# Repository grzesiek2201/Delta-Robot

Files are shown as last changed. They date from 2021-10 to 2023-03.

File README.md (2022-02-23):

# DIY Delta robot

## For your daily needs

**This repo gives a brief (for now) explanation about designing, modeling, building, wiring and programming delta type robot.**

### What does this repository include?
- Application controlling the robot with **live visualization** of the kinematics written in Python
- 3D model of the whole robot, as well as 3D models of all the parts that need to be printed
- BOM
- Build instructions
- Inverse and Forward Kinematics equations with derivation

### Features
- Both online and offline working mode - in offline you can simulate the robot's configuration in different positions
- Bluetooth connection
- Basic manual control by providing x,y,z coordiantes or  \theta_1, \theta_2, \theta_3
- Basic relative position control in Jog mode
- Enabling/disabling motors
- Starting/stoping the program
- Encoders calibration
- Homing
- Changing TCP offset and Jog step
- Changing Z axis limit
- Live robot kinematics visualization
- Live TCP displacement plot in x,y,z coordinates
- Live joints displacement plot in angular coordinates
- Creating and manipulating robot programs, saving, opening and editing. Points can be set either by manually typing in the coordinates or by a teach-in method, in which you hold the robot in a certain position and take it's current configuration as a point's coordiante

### Pictures and screenshots presenting the robot and application
Main screen             |  Collision detection
:-------------------------:|:-------------------------:
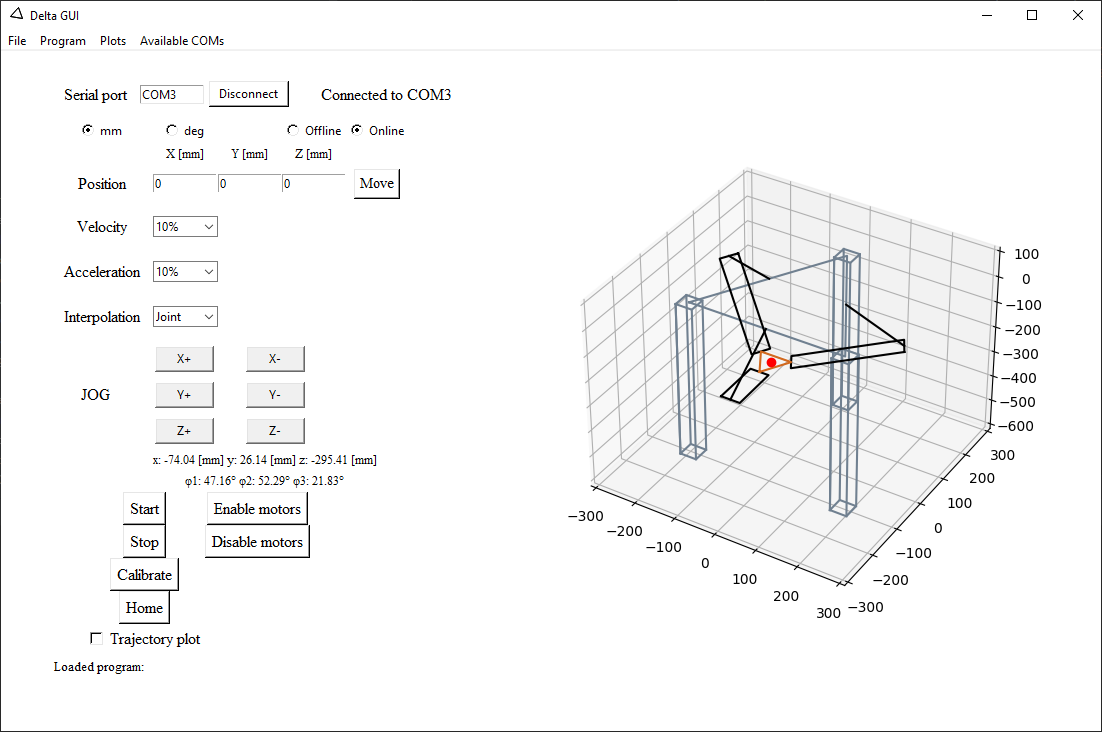
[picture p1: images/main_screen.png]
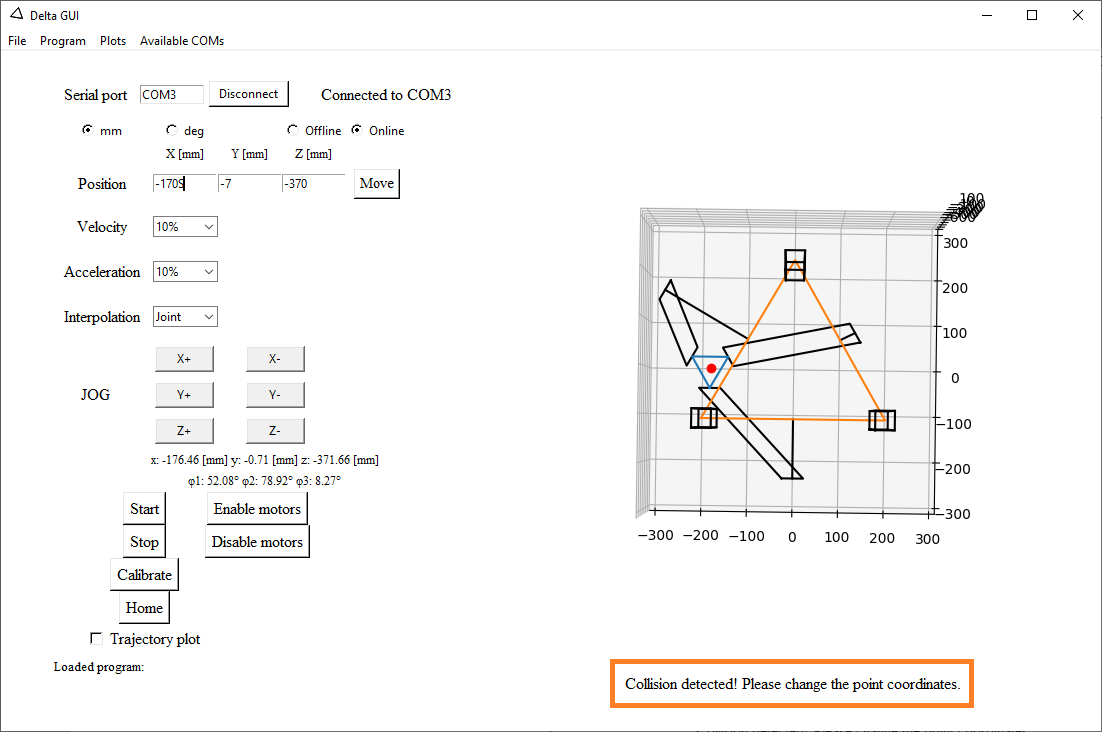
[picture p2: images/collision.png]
  |  
Work envelope             |  Real robot
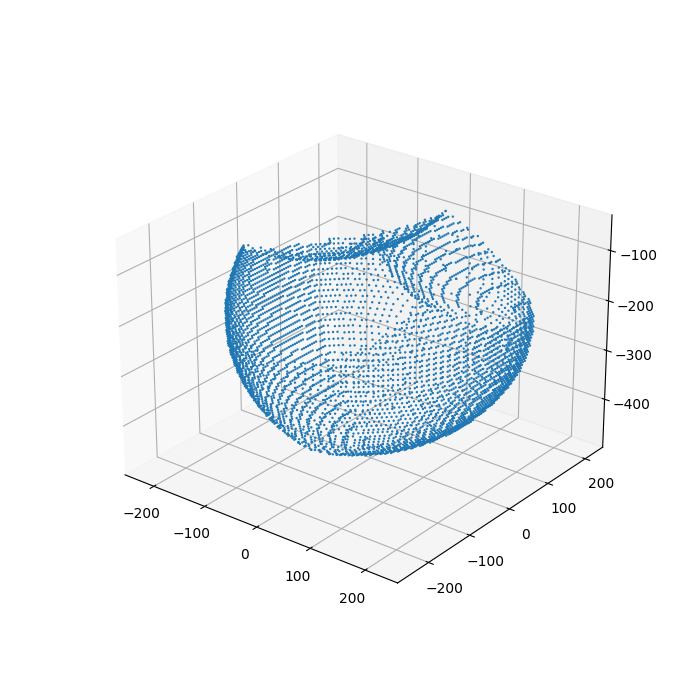
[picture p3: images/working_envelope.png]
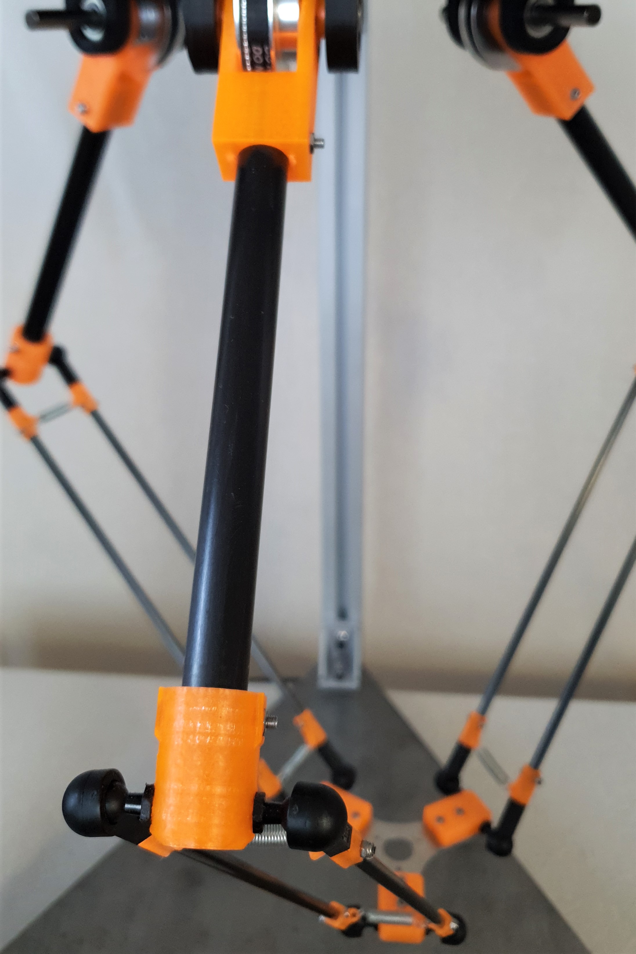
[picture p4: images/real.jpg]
  |  
Joints plot             |  Program creator
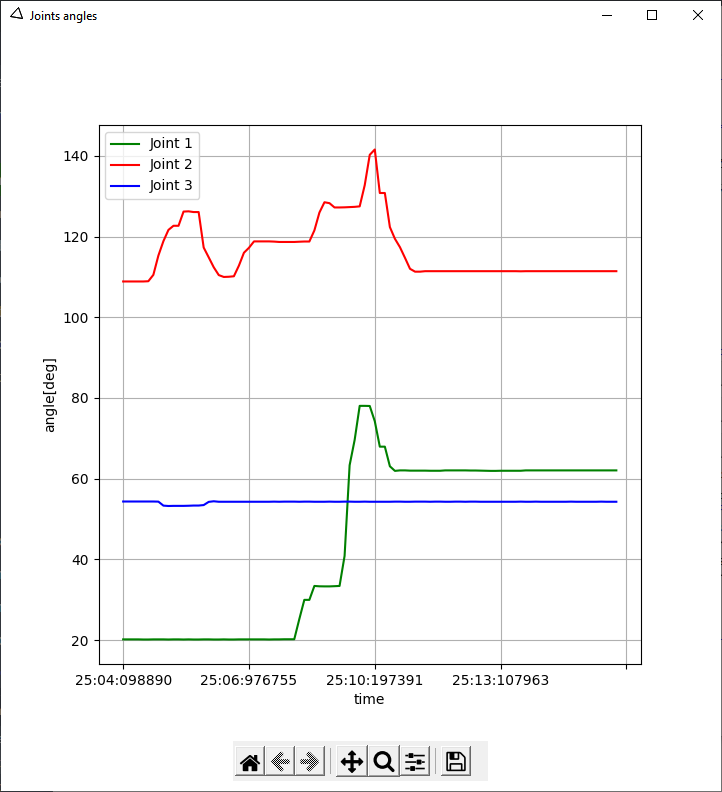
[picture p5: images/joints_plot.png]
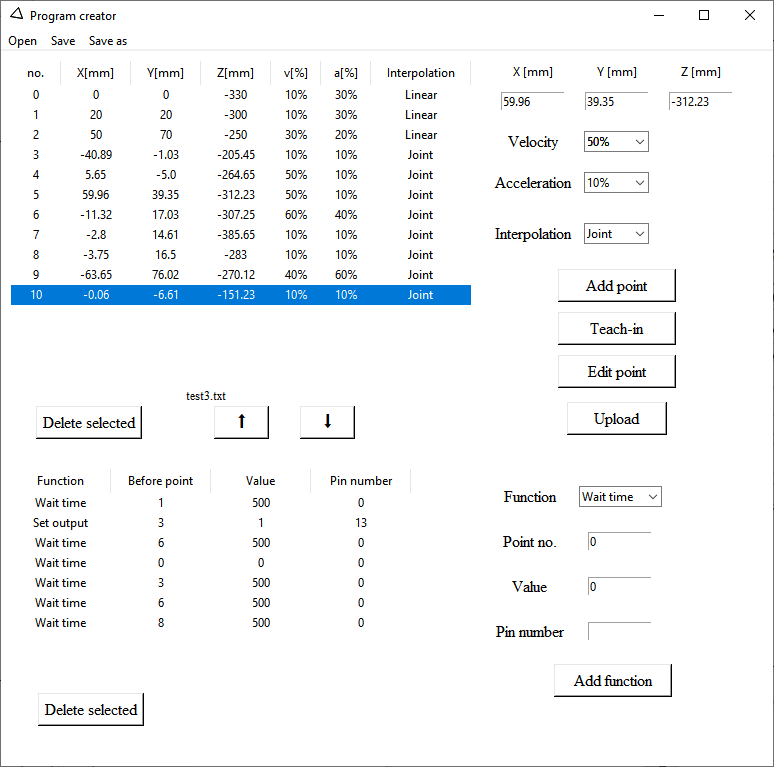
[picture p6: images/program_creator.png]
  |  
Kinematics drawing
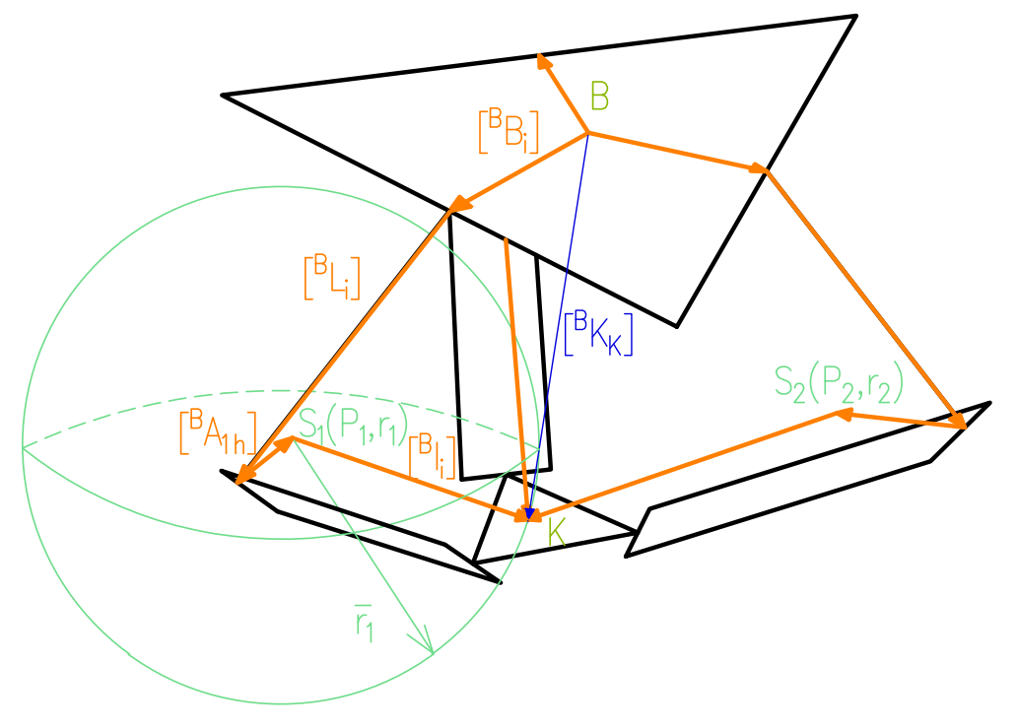
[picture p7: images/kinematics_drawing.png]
 |

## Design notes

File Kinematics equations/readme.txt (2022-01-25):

Kinematics equations necessary to build up the movement and visualization. Both Forward Kinematics and Inverse Kinematics are required.
The required equations are derived in the pdf document.
https://docs.google.com/viewer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

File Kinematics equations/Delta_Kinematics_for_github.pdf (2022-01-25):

# Delta Kinematics for the Delta Robot Project

grzesiek2201

January 2022

## Inverse Kinematics

As inverse kinematics is easier with parallel robots, we’ll start from them. They are also essential for robot control, unlike forward kinematics. The inverse kinematics problem states as follows: given a set of coordinates, find motor angles that correspond to them.

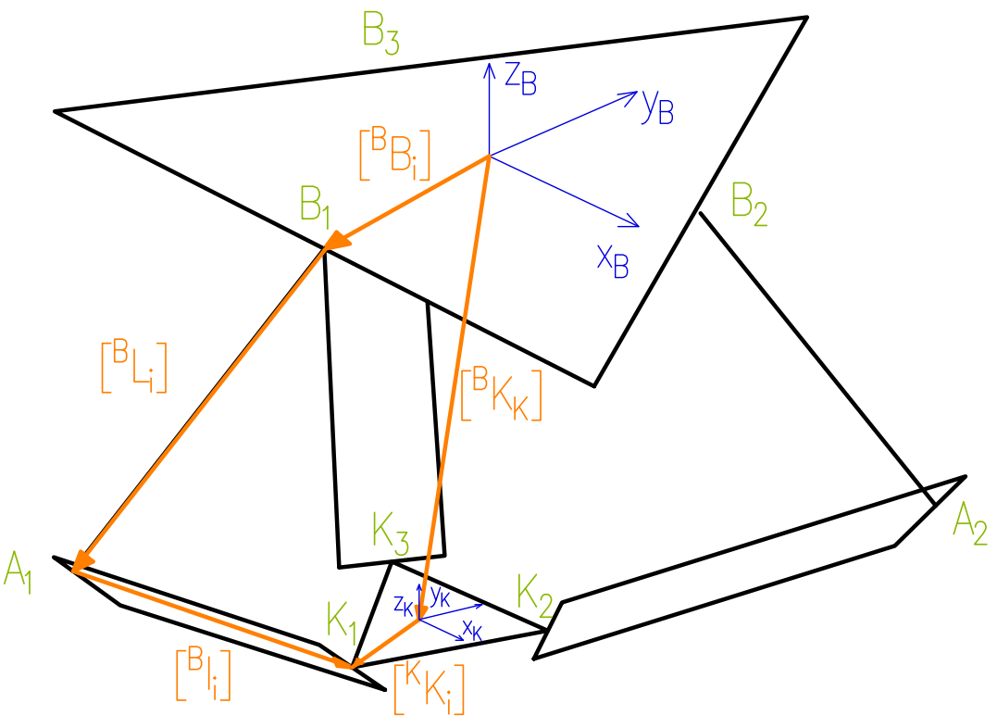
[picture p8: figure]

Figure 1: Kinematic structure of the robot. You can see two coordinate frames, one for the base(B) and one for the effector(K). Vectors drawn will be used in the vector-loop closure equations.

Vector-loop closure equation is as follows:

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
but there is no rotation in the effector

B
KR
= [I3] ,

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
BKK = [x, y, z]

T
(3)

KK1 =

0
−uK
0

KK2 =

sK
2
wK
0

KK3 =

−

sK
2
wK
0
- (4)

BB1 =

0
−wB
0

BB2 =

√
3
2 wB
1
2wB
0

BB3 =

−

√
3
2 wB
1
2wB
0
- (5)

BL1 =

0
−Lcos (θ1)
−Lsin (θ1)

BL2 =

√
3
2

Lcos (θ2)
1/2 Lcos (θ2)
−Lsin (θ2)

BL3 =

−

√
3
2

Lcos (θ3)
1/2 Lcos (θ3)
−Lsin (θ3)
- . | (6)

After substituting (3), (4), (5), (6) into (2):

Bl1 =

x
y + Lcos (θ1) + a
z + Lsin (θ1)

Bl2 =

x −

√
3
2

Lcos (θ2) + b
y −
1/2 Lcos (θ2) + c
z + Lsin (θ2)

Bl3 =

x +

√
3
2

Lcos (θ3) − b
y −

1/2 Lcos (θ3) + c
z + Lsin (θ3)
- ,

where

a = wB − uK, b =

sK
2

−

√
3
2

wB, c = wK −

1
2

wB.

It will be easier to square the vector’s modulus

l

2
i =

Bli

2
= l

2
ix + l

2
iy + l

2
iz.

After substitution we get

x

2 + y

2 + z

2 + L

2 + a

2 + 2ya − l

2 + 2L(y + a) cos θ1 + 2zLsin θ1 = 0 x

2 + y

2 + z

2 + L

2 + b

2 + c

2 + 2xb + 2yc − l

2 − L(

√
3(x + b) + y + c) cos θ2 + 2zLsin θ2 = 0 x

2 + y

2 + z

2 + L

2 + b

2 + c

2 − 2xb + 2yc − l

2 + L(

√
3(x − b) − y − c) cos θ3 + 2zLsin θ3 = 0.

The above system of equations can be simplified into

Ei cos θi + Fi sin θi + Gi = 0,

where:
E1 = 2L(y + a),

E2 = −L(

√
3(x + b) + y + c),

E3 = L(

√
3(x − y − b − c),
F1 = 2zL, | F2 = 2zL, | F3 = 2zL,

G1 = x

2 + y

2 + z

| 2 + L 2 + a | 2 + 2ya − l

2
,

G2 = x

2 + y

2 + z

2 + L

| 2 + b 2 + c | 2 + 2xb + 2yc − l

2
,

G3 = x

2 + y

2 + z

2 + L

| 2 + b 2 + c | 2 − 2xb + 2yc − l

2

The equations can be solved using Weierstrass substitution

Ei

1 − t

2
i
1 + t

2
i
| + Fi
| 2ti 1 + t

2
i
| | + Gi = 0,

Ei(1 − t

2
i

) + Fi(2ti) + Gi(1 + t

2
i

) = 0,

t

2
i

(Gi − Ei) + ti(2Fi) + (Gi + Ei) = 0.

Solution to the quadratic equation:

t1,2 =

−Fi ±

p
G²
i + F

2

i + E²
i
Gi − Ei

,

We get the solution to the inverse kinematics problem:

Θi = 2arctg(ti). | (7)

## Forward Kinematics

The forward kinematics problem states as follows: given a set of motor angles, find effector coordiantes that correspond to them. In order to find a solution to this problem, we must find points of intersection of three spheres, centers of which are located at the elbow joints transposed by the vectors -

BAih
and
radia of which are equal to the length of the forearms. Intersection points are the solution to the forward kinematics problem. The diagram is shown in the Figure 2.
Vectors -

BAih
are equal to:

BA1h =

0
−wB − Lcos(θ1) + uK
−Lsin(θ1)
- ,

BA2h =

√
3
2

(wB + Lcos(θ2)) −

sK
2
1/2(wB + Lcos(θ2)) − wK
−Lsin(θ2)
- ,

BA3h =

−

√
3
2

(wB + Lcos(θ3)) + sK
2
1/2(wB + Lcos(θ3)) − wK
−Lsin(θ3)
- . | (8)

There are three spheres: S1(P1, r1) S2(P2, r2) S3(P3, r3), where points Pi are known and equal to:

P1 =

x1
y1
z1
- , P2 =

x2
y2
z2
- , P3 =

x3
y3
z3

The system of equations describing the presented issue looks as follows:

(x − x1)

2 + (y − y1)

2 + (z − z1)

2 = r

2
1
(x − x2)

2 + (y − y2)

2 + (z − z2)

2 = r

2
2
(x − x3)

2 + (y − y3)

2 + (z − z3)

2 = r

2
3

, K =

x
y
z
- . | (9)


Figure 2: Kinematic diagram with vectors and spheres drawn in order to solve forward kinematics.

After expanding we must substract third equation from the first and second equation, result of which is the system of equations:
a11x + a12y + a13z = b1
a21x + a22y + a23z = b2

,

gdzie
a11 = 2(x3 − x1), | a12 = 2(y3 − y1), | a13 = 2(z3 − z1),
a21 = 2(x3 − x2), | a22 = 2(y3 − y2), | a23 = 2(z3 = z2),

b1 = r

2
1 − r

2
3 − x

2
1 − y

2
1 − z

2
1 + x

2
3 + y

2
3 + z

2/3, b2 = r

2
2 − r

2
3 − x

2
2 − y

2
2 − z

2
2 + x

2
3 + y

2
3 + z

2/3.

The above system of equations has been solved by determining z:

z =

b1
a13
− | a12 a13 y −

a11
a13

x

z =

b2
a23
− | a22 a23 y −

a21
a23

x

(10)

After substracting second equation from the first equation:

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
where
a1 =

a11

a13

−

a21

a23

, a2 =

a22

a23

−

a12

a13

, a3 =

b1

a13

−

b2
a23

We get
x = f(y) = a4y + a5,

where
a4 =

a2
a1

, a5 =

a3
a1

The dependency of x(y) has been determined. Next we need to substitute it into one of the equations in the (10). We get:
z = f(y) = a6y + a7,

where
a6 =

−a21a4 − a22

a23

, a7 =

b2 − a21a5

a23

The dependency z(y) has been determined, so we need to substitue it into one of the sphere equations. We get
ay² + by + c = 0, | (11)

where

a = a

2
4 + 1 + a

2/6, b = 2a4(a5 − a1) + 2a6(a7 − z1) − 2y1,

c = a5(a5 − 2x1) + a7(a7 − 2z1) + x

| 2 1 + y
| 2 1 + z
| 2 1 − r 2/1.

The equation (11) is an quadratic formula, solution to which is as follows:

x+ = a4y+ + a5

y+ =

−b+

√
b

2−4ac
2a

z+ = a6y+ + a7

,

x− = a4y− + a5

y− =

−b−

√
b

2−4ac
2a

z− = a6y− + a7

,

K+ =

x+
y+
z+
- , K− =

x−
y−
z−

In order for the real solutions to exist, the ∆ ≥ 0 must exist. If calculated ∆ will be smaller than zero, it suggests that an error occured when reading the motor angles, as motor angles cannot have irrational values.
Now we need to consider singularities of the given solution. It has no solutions, when at least one of the below condition is met:
a13 = 0, | (12)

a23 = 0, | (13)
a1 = 0, | (14)
a = 0. | (15)

Condition (14) is met, when

a1 =

a11

a13

−

a21

a23

=

(x3 − x1)(z3 − z2) − (x3 − x2)(z3 − z1) (z3 − z1)(z3 − z2)

= 0

⇕
x3 − x1
z3 = z1

=

x3 − x2
z3 − z2

Let z3 = x3 = 0 , so the point 3 lies in the middle of the coordinate system. Then x1
z1

=

x2
z2

This condition is only met when three points, which are the centers of the spheres, are collinear in the XZ plane. That is why for a valid geometry, this singularity never occurs.
Condition (15) is met, when

a = a

2
4 + a

2
6 + 1 = 0 ⇔ a

2
4 + a

2
6 = −1.

For real a4 and a6 this condition cannot be met, that is why it does not have to be considered in the overall solution.
Conditions (12) and (13) are met, when z3 − z1 = 0 and z3 − z2 = 0. It is only possible in a configuration in which the angle of the first arm is equal to the angle of the third arm and when angle of the second arm is equal to the angle of the third arm. This is possible under typical operation and has to be accounted for in the general solution. In order to get rid of the singularities the solution to the problem, when z1 = z2 = z3 =: zn, has been found. We start from the same equations for the intersection of three spheres as before

(x − x1)

2 + (y − y1)

2 + (z − zn)

2 = r

2
1
(x − x2)

2 + (y − y2)

2 + (z − zn)

2 = r

2
2
(x − x3)

2 + (y − y3)

2 + (z − zn)

2 = r
2/3.

After multiplication and substitution of the third equation for the first and the second equation we get
ax + by = c
dx + ey = f

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
af−cd
ae−bd

⇒

(
x =

ce−bf
ae−bd
y =

af−cd
ae−bd ,

where
a = 2(x3 − x1), | b = 2(y3 = y1), | c = r
| | 2 1 − r

2
3 − x

2
1 − y

2
1 + x

2
3 + y

2/3,

d = 2(x3 − x2), | e = 2(y3 − y2), | f = r

2
2 − r

2
3 − x

2
2 − y

2
2 + x

2
3 + y

2/3.

The calculated x and y have been substituted into the first equation from the 9 system of equations:

Az² + Bz + C = 0,

where
| A = 1,
B = −2zn,
| C = x 2 + y 2 + x
| 2 1 + y

2
| | 1 − 2xx1 − r

2
1 + z

2
n

The solution to the forward kinematics problem is as follows:

x =

ce−bf
ad−bd

y =

af−cd
ae−bd

z =

−B±

√
B²−4C

We also have to investigate the singularities of the solution:

ae − bd = 0,
∆ < 0 ⇔ B² − 4AC = 0.

The first of the singularities has been expanded below:

ae − bd = 0 ⇔ x3−x1
y3−y1

=

x3−x2
y3−y2

The above equality is met only when centers of the spheres lay on the XY plane and are collinear. For a symmetric configuration of the robot, this singularity does not have to be considered in the general solution.
The second of the singularities is met when

B

2 − 4AC = 0 ⇔ r

2
1 < (x − x1)

2 + (y − y1)

2

The above inequality cannot be met, as we know the the below equation is true

(x − x1)

2 + (y − y1)

2 = r
2/1.

There is also a situation in which two of the three spheres are position on the same height. Instead of deriving further equations, which would let us get rid of this singularity, it is possible to add a very small value to one of the sphere’s height when the situation occurs. It does not influence the accuracy of the visualization and control in a visible way, but it does simplify the theoretical considerations.

## Visualization

The calculation will based on the angular position of the motors measured by enoders as well as equations derived below. In order to create the visualization, we must know coordinates of all the points of a drawn line. Objects that will be drawn as a line are: each of the arms, each of the forearms, base, and effector. Each of the legs will be a simple prism, thus their representation will consist of two bases and four edges. The base vertices are described with vectors

Bb1 =

sB
2
−wB
0
- ,

Bb2 =

0
uK
0
- ,

Bb3 =

−

sB
2
−wB
0
- . | (16)

The vectors below -
BAi
are describing position of the elbow joints in respect to the base B:

BA1 =

0
−wB − Lcos(θ1)
−Lsin(θ1)
- ,

BA2 =

√
3
2

(wB + Lcos(θ2))
1/2(wB + Lcos(θ2))
−Lsin(θ2)
- ,

BA3 =

−

√
3
2

(wB + Lcos(θ3))
1/2(wB + Lcos(θ3))
−Lsin(θ3)
- . | (17)

Vectors -
BKi
describe the position of the effector’s joints in respect to the base B:

BK1 =

x
−

sK
2 + y
z
- ,

BK2 =

sK
2 + x
wK + y
z
- ,

BK3 =

−

sK
2 + x
wK + y
z
- . | (18)

Vectors -
BBi
describe the position of the arm joints in respect to the base B:

BB1 =

0
−wB
0
- ,

BB2 =

√
3
2 wB
1
2wB
0
- ,

BB3 =

−

√
3
2 wB
1
2wB
0
- . | (19)

Vectors -

BAij
describe the position of the elbow joints transposed by a vector equal to their width, in respect to the base B:

BA11 =

−

ew
2
−wB − Lcos(θ1)
−Lsin(θ1)
- ,

BA12 =

ew
2
−wB − Lcos(θ1)
−Lsin(θ1)
- ,

BA21 =

√
3
2

(wB + Lcos(θ2)) + ew
4
1/2(wB + Lcos(θ2)) −

√
3
4

ew
−Lsin(θ2)

- ,

BA22 =

√
3
2

(wB + Lcos(θ2)) −

ew
4
1/2(wB + Lcos(θ2)) +

√
3
4

ew
−Lsin(θ2)

- ,

BA31 =

−

√
3
2

(wB + Lcos(θ3)) + ew
4
1/2(wB + Lcos(θ3)) +

√
3
4

ew
−Lsin(θ3)

- ,

BA32 =

−

√
3
2

(wB + Lcos(θ3)) −

ew
4
1/2(wB + Lcos(θ3)) −

√
3
4

ew
−Lsin(θ3)

Vectors -
BKij
describe the position of the efector joints transpoed by the same vector as above, in respect to the base B:

BK11 =

x −

ew
2
−

sK
2 + y
z
- ,

BK12 =

x +

ew
2
−

sK
2 + y
z
- ,

BK21 =

sK
2 + x +

ew
4
wK + y −

√
3
4

ew
z
- ,

BK21 =

sK
2 + x −

ew
4
wK + y +

√
3
4

ew
z
- ,

BK31 =

−

sK
2 + x +

ew
4
wK + y +

√
3
4

ew
z
- ,

BK32 =

−

sK
2 + x −

ew
4
wK + y −

√
3
4

ew
z

We know all the points necessary to create the visualization of the kinematic structure of the robot.

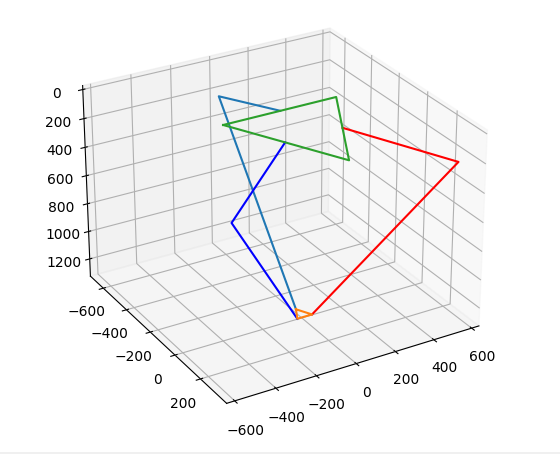
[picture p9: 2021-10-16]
DeltaApp/src/plot_example.png

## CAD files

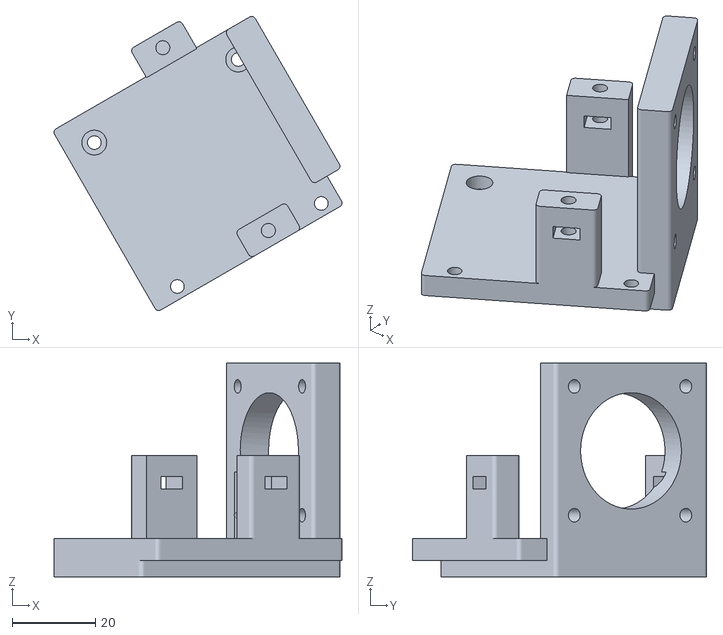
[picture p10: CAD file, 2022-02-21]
stl_dxf/motor_mount.stl
69.3 x 70.8 x 51.5

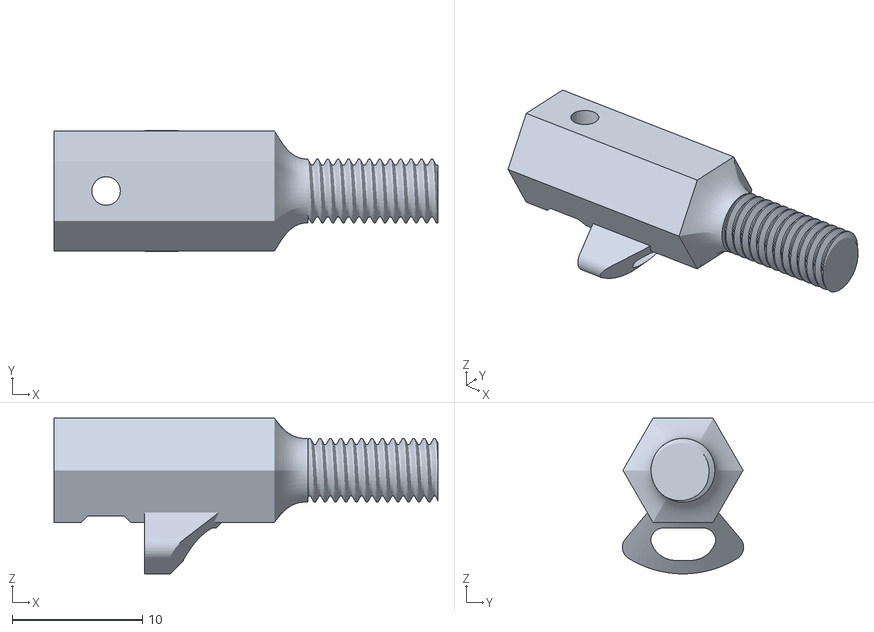
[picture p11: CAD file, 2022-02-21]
stl_dxf/elbow_joint_1.stl
29.5 x 9.32 x 12.0

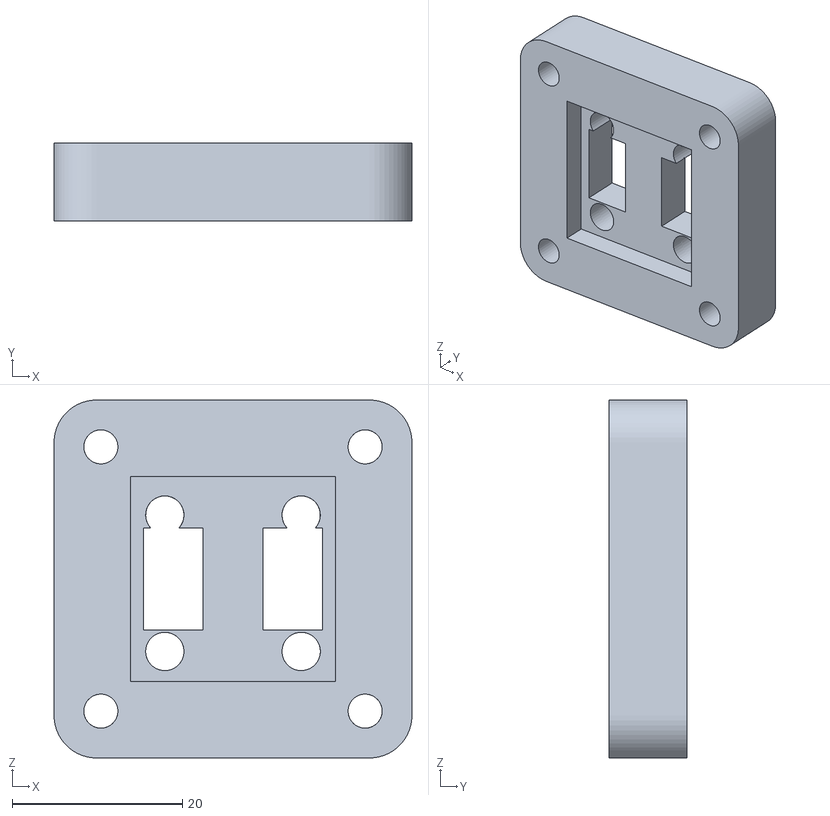
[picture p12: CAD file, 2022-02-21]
stl_dxf/as5600_encoder_mount.stl
42.0 x 9.20 x 42.0

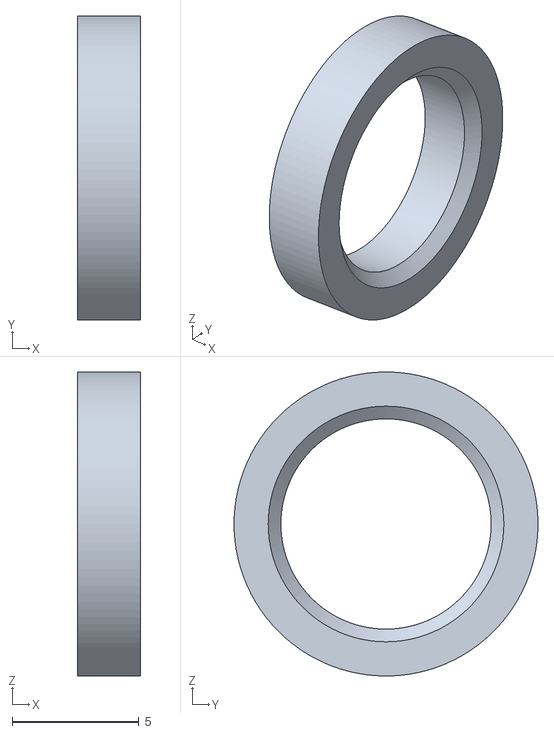
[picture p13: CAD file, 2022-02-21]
stl_dxf/shoulder_mount_spacer.stl
2.50 x 12.0 x 12.0

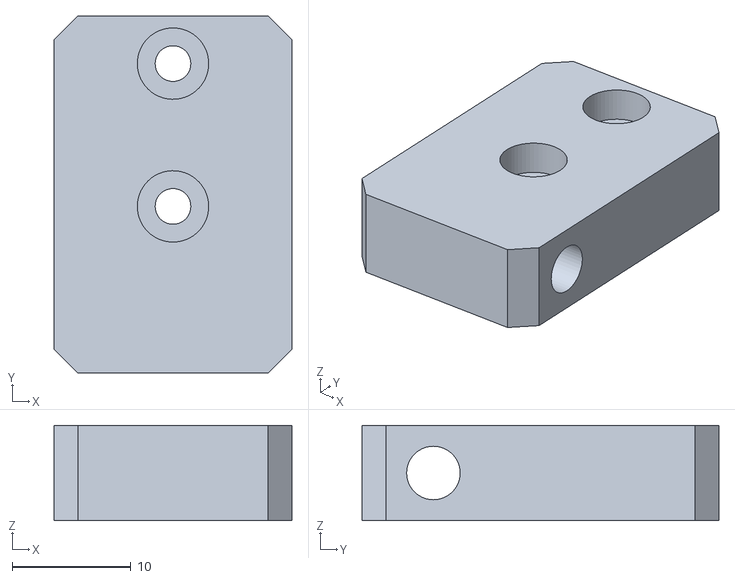
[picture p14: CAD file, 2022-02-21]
stl_dxf/effector_forearm_mounting.stl
20.0 x 30.0 x 8.00

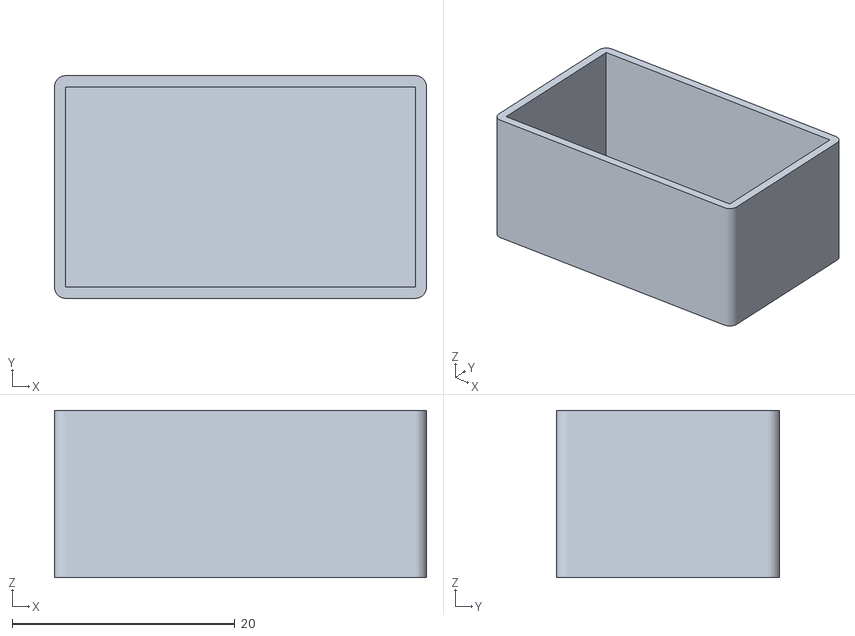
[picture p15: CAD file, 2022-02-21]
stl_dxf/multiplexer_enclosure.stl
33.4 x 20.0 x 15.0

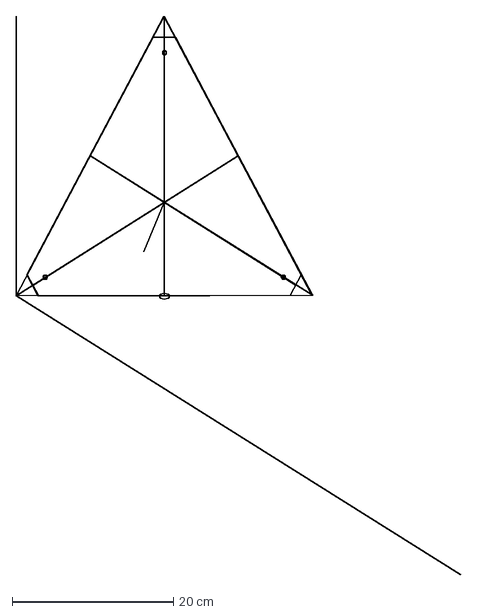
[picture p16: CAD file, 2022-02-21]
stl_dxf/top_plate.dxf
55.1 x 69.3 cm

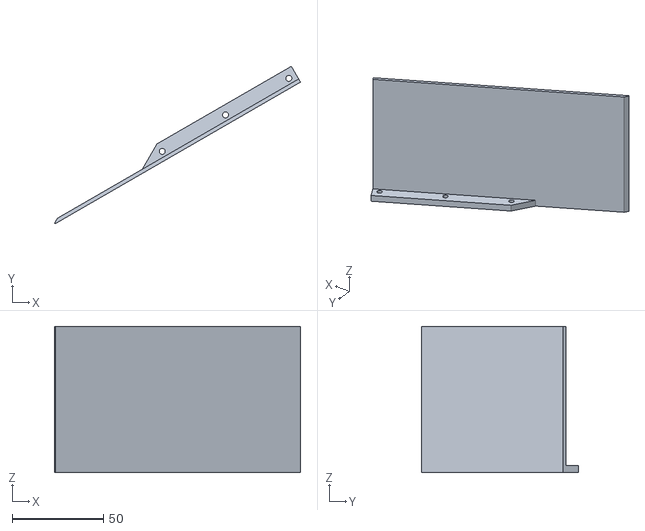
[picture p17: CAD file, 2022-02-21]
stl_dxf/wall_no_fan.stl
134.7 x 86.2 x 80.0

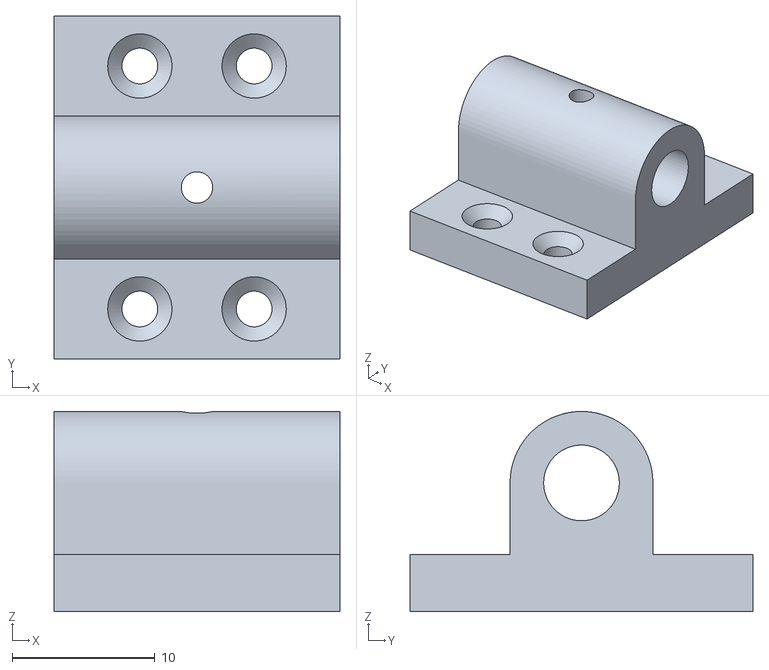
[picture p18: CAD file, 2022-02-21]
stl_dxf/carbon_tube_holder_opened.stl
20.0 x 24.0 x 14.0

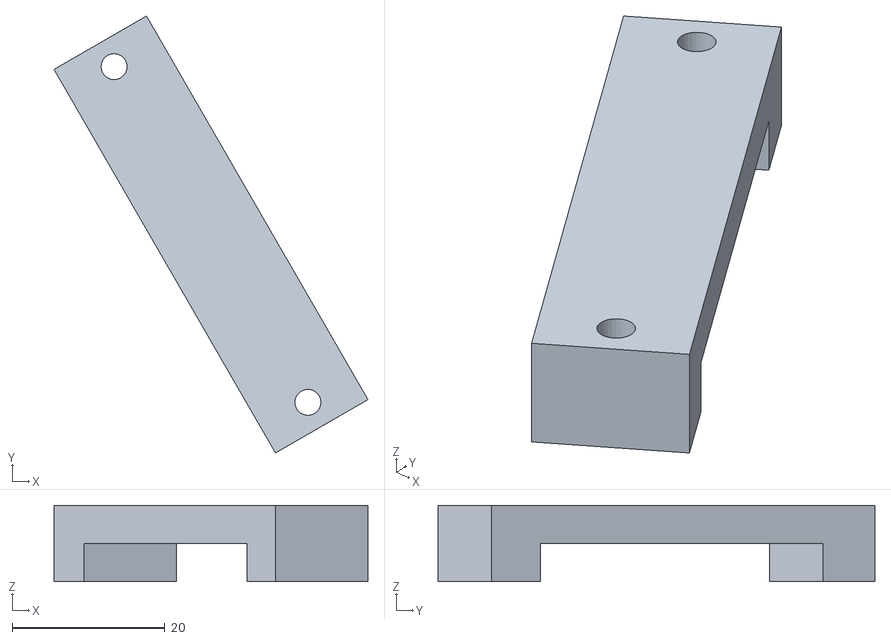
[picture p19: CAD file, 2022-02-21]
stl_dxf/motor_mount_holder.stl
41.1 x 57.3 x 10.0

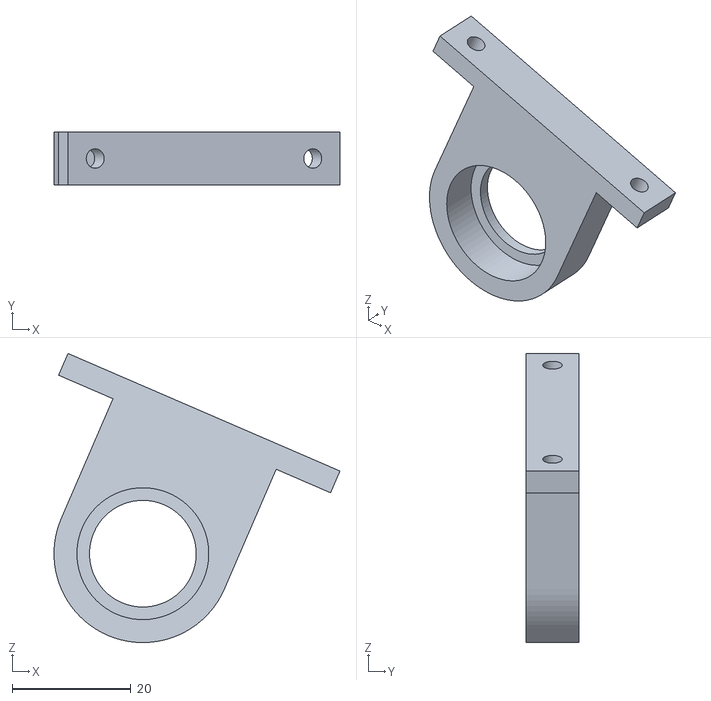
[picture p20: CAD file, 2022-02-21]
stl_dxf/bearing_mount.stl
48.3 x 9.00 x 48.8

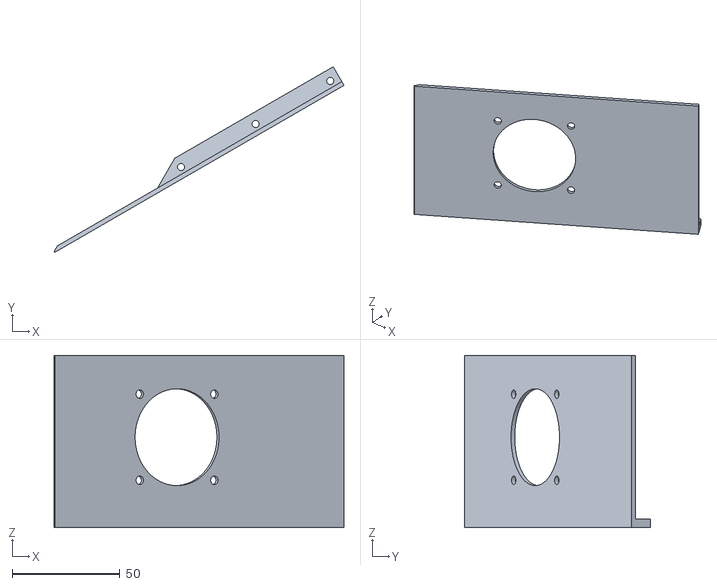
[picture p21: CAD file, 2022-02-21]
stl_dxf/wall_w_fan_1.stl
134.7 x 86.2 x 80.0

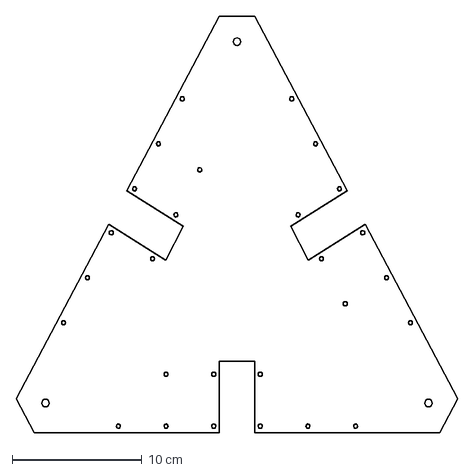
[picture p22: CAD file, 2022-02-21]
stl_dxf/bottom_plate.dxf
34.0 x 32.0 cm

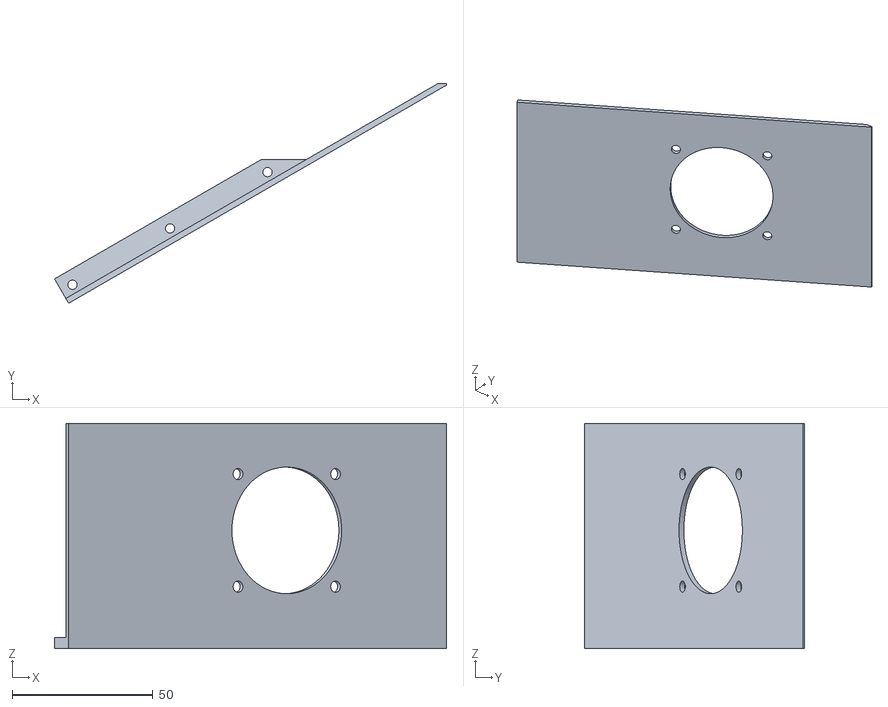
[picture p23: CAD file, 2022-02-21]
stl_dxf/wall_w_fan_2.stl
139.2 x 78.0 x 80.0

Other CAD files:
stl_dxf/effector_plate.dxf
stl_dxf/shoulder_mount.stl
stl_dxf/carbon_tube_holder_closed.stl
stl_dxf/elbow_joint_2.stl

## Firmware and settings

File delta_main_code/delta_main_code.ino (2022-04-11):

#include <ArduinoJson.h>
#include <Wire.h>
#include "inverse_kin.h"

#include "SSD1306Ascii.h"
#include "SSD1306AsciiAvrI2c.h"

#include "FlexyStepper.h"
#include <SPI.h>
#include <SD.h>

StaticJsonDocument<64> doc_rx;
StaticJsonDocument<64> doc_tx;
char output[64];

// oled
#define RST_PIN -1
#define OLED_PIN 4
SSD1306AsciiAvrI2c oled;

#define TIMEOUT 5000
#define BAUDRATE 115200

#define ENC_COMPENSATE_1 120
#define ENC_COMPENSATE_2 148
#define ENC_COMPENSATE_3 158

#define TCAADDR 0x70
#define address 0x36

#define NO_POINTS 50

#define SERVO_PIN 63

// flexystepper
FlexyStepper stepper1;
FlexyStepper stepper2;
FlexyStepper stepper3;

// SD card
File my_file;
String buffer;
// #define INTERVALS_SIZE 400
// int velocities_1[INTERVALS_SIZE];
// int velocities_2[INTERVALS_SIZE];
// int velocities_3[INTERVALS_SIZE];
int velocities[3];

// reading messages
const byte numChars = 128;
char receivedChars[numChars];
boolean newData = false;

// communication
uint8_t index_of_point;
uint8_t interpolation_array[NO_POINTS];
uint8_t velocity_array[NO_POINTS];
uint8_t acceleration_array[NO_POINTS];
float x_array[NO_POINTS];
float y_array[NO_POINTS];
float z_array[NO_POINTS];

// additional functions
bool start = false;
bool teach_in_cmd = false;
uint8_t enable_cmd = 0;
uint8_t gripper_state = 0;
uint16_t program_length = 0;
byte mode = 0;
bool receive_in_progress = false;

// inverse kinematics
inverse_kin inverse_kin;
float position_array[3];
float previous_fi_array[3];
float fi_array[3];
short int steps_to_make_x[NO_POINTS];
short int steps_to_make_y[NO_POINTS];
short int steps_to_make_z[NO_POINTS];

// encoders
int low_byte;                        //raw angle 7:0
word high_byte;                      //raw angle 7:0 and 11:8
int raw_angle;                       //final raw angle
float deg_angle[3];                     //raw angle in degrees (360/4096 * [value between 0-4095])

int quadrantNumber[3], previousquadrantNumber[3]; //quadrant IDs
float numberofTurns[3] = {0, 0, 0}; //number of turns
float correctedAngle[3] = {0, 0, 0}; //tared angle - based on the startup value
float startAngle[3] = {0, 0, 0}; //starting angle
float totalAngle[3] = {0, 0, 0}; //total absolute angular displacement
float previoustotalAngle[3] = {0, 0, 0}; //for the display printing


// For RAMPS 1.4
#define X_DIR_PIN          55
#define X_STEP_PIN         54
#define X_ENABLE_PIN       38

#define Y_DIR_PIN          61
#define Y_STEP_PIN         60
#define Y_ENABLE_PIN       56

#define Z_DIR_PIN          48
#define Z_STEP_PIN         46
#define Z_ENABLE_PIN       62

#define X_STEP_HIGH             PORTF |=  0b00000001;
#define X_STEP_LOW              PORTF &= ~0b00000001;

#define Y_STEP_HIGH             PORTF |=  0b01000000;
#define Y_STEP_LOW              PORTF &= ~0b01000000;

#define Z_STEP_HIGH             PORTL |=  0b00001000;
#define Z_STEP_LOW              PORTL &= ~0b00001000;

#define TIMER1_INTERRUPTS_ON    TIMSK1 |=  (1 << OCIE1A);
#define TIMER1_INTERRUPTS_OFF   TIMSK1 &= ~(1 << OCIE1A);


struct stepperInfo {
  // externally defined parameters
  float acceleration;
  volatile unsigned long minStepInterval; // ie. max speed, smaller is faster
  void (*dirFunc)(int);
  void (*stepFunc)();

  // derived parameters
  unsigned int c0;                // step interval for first step, determines acceleration
  long stepPosition;              // current position of stepper (total of all movements taken so far)

  // per movement variables (only changed once per movement)
  volatile int dir;                        // current direction of movement, used to keep track of position
  volatile unsigned int totalSteps;        // number of steps requested for current movement
  volatile bool movementDone = false;      // true if the current movement has been completed (used by main program to wait for completion)
  volatile unsigned int rampUpStepCount;   // number of steps taken to reach either max speed, or half-way to the goal (will be zero until this number is known)
  volatile unsigned long estStepsToSpeed;  // estimated steps required to reach max speed
  volatile unsigned long estTimeForMove;   // estimated time (interrupt ticks) required to complete movement
  volatile unsigned long rampUpStepTime;
  volatile float speedScale;               // used to slow down this motor to make coordinated movement with other motors

  // per iteration variables (potentially changed every interrupt)
  volatile unsigned int n;                 // index in acceleration curve, used to calculate next interval
  volatile float d;                        // current interval length
  volatile unsigned long di;               // above variable truncated
  volatile unsigned int stepCount;         // number of steps completed in current movement
};

void xStep() {
  X_STEP_HIGH
  X_STEP_LOW
}
void xDir(int dir) {
  digitalWrite(X_DIR_PIN, dir);
}

void yStep() {
  Y_STEP_HIGH
  Y_STEP_LOW
}
void yDir(int dir) {
  digitalWrite(Y_DIR_PIN, dir);
}

void zStep() {
  Z_STEP_HIGH
  Z_STEP_LOW
}
void zDir(int dir) {
  digitalWrite(Z_DIR_PIN, dir);
}

void resetStepperInfo( stepperInfo& si ) {
  si.n = 0;
  si.d = 0;
  si.di = 0;
  si.stepCount = 0;
  si.rampUpStepCount = 0;
  si.rampUpStepTime = 0;
  si.totalSteps = 0;
  si.stepPosition = 0;
  si.movementDone = false;
}

#define NUM_STEPPERS 3

volatile stepperInfo steppers[NUM_STEPPERS];

struct pointFunction{
  bool func_type[3];
  unsigned int value[3];
  uint8_t pin_no[3];
};

void reset_point_functions(pointFunction* pt);
void reset_point_functions(pointFunction* pt){
  for(int i=0; i < NO_POINTS; i++){
    for(int j = 0; j < 3; j++){
      pt[i].func_type[j] = 0;
      pt[i].value[j] = 0;
      pt[i].pin_no[j] = 0;    
    } 
  }     
}

pointFunction point_functions[NO_POINTS];

void showOnScreen(String text, bool show_coordinates = 0, int number_of_coordinate = 0);

void setup() {
  Serial.begin(BAUDRATE);
  Serial2.begin(BAUDRATE);
  Wire.begin();

  //oled
  tcaselect(OLED_PIN);
  #if RST_PIN >= 0
  oled.begin(&Adafruit128x64, 0x3C, RST_PIN);
  #else // RST_PIN >= 0
  oled.begin(&Adafruit128x64, 0x3C);
  #endif // RST_PIN >= 0
  // Call oled.setI2cClock(frequency) to change from the default frequency.

  oled.setFont(Arial_bold_14);
  oled.clear();

  oled.set2X();
  showOnScreen("is delta");
  oled.set1X();

  // flexystepper
  stepper1.connectToPins(X_STEP_PIN, X_DIR_PIN);
  stepper2.connectToPins(Y_STEP_PIN, Y_DIR_PIN);
  stepper3.connectToPins(Z_STEP_PIN, Z_DIR_PIN);
  stepper1.setAccelerationInStepsPerSecondPerSecond(3000);
  stepper2.setAccelerationInStepsPerSecondPerSecond(3000);
  stepper3.setAccelerationInStepsPerSecondPerSecond(3000);
  
  // SD card
  uint16_t start_time = millis();
  uint16_t init_time = 0;
  uint8_t timeout = 2000;
  while(!SD.begin(53) && init_time < timeout)
    init_time = millis() - start_time;
  
  // readIntervals(velocities_1, velocities_2, velocities_3);  // read intervals from SD card


  startAngle[0] = ENC_COMPENSATE_1; 
  startAngle[1] = ENC_COMPENSATE_2; 
  startAngle[2] = ENC_COMPENSATE_3;

  readRawAngle(1);
  readRawAngle(2);  
  readRawAngle(3);   
  correctAngle(1);
  correctAngle(2);
  correctAngle(3);
  checkQuadrant(1);
  checkQuadrant(2);
  checkQuadrant(3);
  fi_array[0] = totalAngle[0];
  fi_array[1] = totalAngle[1];
  fi_array[2] = totalAngle[2];

  pinMode(X_STEP_PIN,   OUTPUT);
  pinMode(X_DIR_PIN,    OUTPUT);
  pinMode(X_ENABLE_PIN, OUTPUT);

  pinMode(Y_STEP_PIN,   OUTPUT);
  pinMode(Y_DIR_PIN,    OUTPUT);
  pinMode(Y_ENABLE_PIN, OUTPUT);

  pinMode(Z_STEP_PIN,   OUTPUT);
  pinMode(Z_DIR_PIN,    OUTPUT);
  pinMode(Z_ENABLE_PIN, OUTPUT);

  digitalWrite(X_ENABLE_PIN, HIGH);
  digitalWrite(Y_ENABLE_PIN, HIGH);
  digitalWrite(Z_ENABLE_PIN, HIGH);

  noInterrupts();
  TCCR1A = 0;
  TCCR1B = 0;
  TCNT1  = 0;

  OCR1A = 1000;                             // compare value
  TCCR1B |= (1 << WGM12);                   // CTC mode
  TCCR1B |= ((1 << CS11) | (1 << CS10));    // 64 prescaler
  interrupts();

  steppers[0].dirFunc = xDir;
  steppers[0].stepFunc = xStep;
  steppers[0].acceleration = 500;
  steppers[0].minStepInterval = 30;

  steppers[1].dirFunc = yDir;
  steppers[1].stepFunc = yStep;
  steppers[1].acceleration = 500;
  steppers[1].minStepInterval = 30;

  steppers[2].dirFunc = zDir;
  steppers[2].stepFunc = zStep;
  steppers[2].acceleration = 500;
  steppers[2].minStepInterval = 30;

  while(Serial2.available()){ 
    char clear_input = Serial2.read();
    }
}

void resetStepper(volatile stepperInfo& si) {
  si.c0 = si.acceleration;
  si.d = si.c0;
  si.di = si.d;
  si.stepCount = 0;
  si.n = 0;
  si.rampUpStepCount = 0;
  si.movementDone = false;
  si.speedScale = 1;

  float a = si.minStepInterval / (float)si.c0;
  a *= 0.676;

  float m = ((a*a - 1) / (-2 * a));
  float n = m * m;

  si.estStepsToSpeed = n;
}

volatile uint8_t remainingSteppersFlag = 0;

float getDurationOfAcceleration(volatile stepperInfo& s, unsigned int numSteps) {

  return s.c0 * sqrt(1.38 * numSteps + numSteps);
  
}

void prepareMovement(int whichMotor, long steps) {
  if (steps == 0) {return;}  
  volatile stepperInfo& si = steppers[whichMotor];
  si.dirFunc( steps < 0 ? HIGH : LOW );
  si.dir = steps > 0 ? 1 : -1;
  si.totalSteps = abs(steps);
  resetStepper(si);
  
  remainingSteppersFlag |= (1 << whichMotor);

  unsigned long stepsAbs = abs(steps);

  if ( (2 * si.estStepsToSpeed) < stepsAbs ) {
    // there will be a period of time at full speed
    unsigned long stepsAtFullSpeed = stepsAbs - 2 * si.estStepsToSpeed;
    float accelDecelTime = getDurationOfAcceleration(si, si.estStepsToSpeed);
    si.estTimeForMove = 2 * accelDecelTime + stepsAtFullSpeed * si.minStepInterval;
  }
  else {
    // will not reach full speed before needing to slow down again
    float accelDecelTime = getDurationOfAcceleration( si, stepsAbs / 2 );
    si.estTimeForMove = 2 * accelDecelTime;
  }
}

volatile uint8_t nextStepperFlag = 0;

void setNextInterruptInterval() {

  bool movementComplete = true;

  unsigned long mind = 999999;
  for (int i = 0; i < NUM_STEPPERS; i++) {
    if ( ((1 << i) & remainingSteppersFlag) && steppers[i].di < mind ) {
      mind = steppers[i].di;
    }
  }

  nextStepperFlag = 0;
  for (int i = 0; i < NUM_STEPPERS; i++) {
    if ( ! steppers[i].movementDone )
      movementComplete = false;
    if ( ((1 << i) & remainingSteppersFlag) && steppers[i].di == mind )
      nextStepperFlag |= (1 << i);
  }

  if ( remainingSteppersFlag == 0 ) {
    TIMER1_INTERRUPTS_OFF
    OCR1A = 65500;
  }

  OCR1A = mind;
}

ISR(TIMER1_COMPA_vect)
{
  unsigned int tmpCtr = OCR1A;

  OCR1A = 65500;

  for (int i = 0; i < NUM_STEPPERS; i++) {

    if ( ! ((1 << i) & remainingSteppersFlag) )
      continue;

    if ( ! (nextStepperFlag & (1 << i)) ) {
      steppers[i].di -= tmpCtr;
      continue;
    }

    volatile stepperInfo& s = steppers[i];

    if ( s.stepCount < s.totalSteps ) {
      s.stepFunc();
      s.stepCount++;
      s.stepPosition += s.dir;
      if ( s.stepCount >= s.totalSteps ) {
        s.movementDone = true;
        remainingSteppersFlag &= ~(1 << i);
      }
    }

    if ( s.rampUpStepCount == 0 ) {
      s.n++;
      s.d = s.d - (2 * s.d) / (4 * s.n + 1);
      if ( s.d <= s.minStepInterval ) {
        s.d = s.minStepInterval;
        s.rampUpStepCount = s.stepCount;
      }
      if ( s.stepCount >= s.totalSteps / 2 ) {
        s.rampUpStepCount = s.stepCount;
      }
      s.rampUpStepTime += s.d;
    }
    else if ( s.stepCount >= s.totalSteps - s.rampUpStepCount ) {
      s.d = (s.d * (4 * s.n + 1)) / (4 * s.n + 1 - 2);
      s.n--;
    }

    s.di = s.d * s.speedScale; // integer
  }

  setNextInterruptInterval();

  TCNT1  = 0;
}


void runAndWait() {
  adjustSpeedScales();
  setNextInterruptInterval();
  TIMER1_INTERRUPTS_ON
  while ( remainingSteppersFlag )
  {
    readEncoders();
    // delayMicroseconds(500000);
    sendEncodersData();
    // delayMicroseconds(1000);
  };
  remainingSteppersFlag = 0;
  nextStepperFlag = 0;
}

void adjustSpeedScales() {
  float maxTime = 0;
  
  for (int i = 0; i < NUM_STEPPERS; i++) {
    if ( ! ((1 << i) & remainingSteppersFlag) )
      continue;
    if ( steppers[i].estTimeForMove > maxTime )
      maxTime = steppers[i].estTimeForMove;
  }

  if ( maxTime != 0 ) {
    for (int i = 0; i < NUM_STEPPERS; i++) {
      if ( ! ( (1 << i) & remainingSteppersFlag) )
        continue;
      steppers[i].speedScale = maxTime / steppers[i].estTimeForMove;
    }
  }
}


void loop() {
  int8_t point_number = 0;
  readEncoders();
  sendEncodersData();
  fi_array[0] = totalAngle[0];
  fi_array[1] = totalAngle[1];
  fi_array[2] = totalAngle[2];
  unsigned long time = millis();
  unsigned long receive_time = millis();  
  do {
      mode = readMode();  // read the message mode
      if (mode >= '0'){   // if the message mode is an information message, process it
        receive_in_progress = true; // make sure all the message will be received
        delay(10);
        recvWithStartEndMarkers();  // read the message
        if (newData == true){ // if the message is read
          newData = false;  // reset the new data bool
          deserializeSerial();
          switch(mode) {
            case '0':
              start = doc_rx["start"];
              break;

            case '1': // read program's points
              {
              showOnScreen("Reading program...");             
              reset_point_functions(point_functions);   // reset additional functions              
              readPoint();
              Serial2.print("OK");
              Serial2.flush();
              }
              program_length = index_of_point + 1;              
              break;
            case '2': // manual move
              readPoint();

              showOnScreen("Moving to point ", 1, 0);
                           
              changeParameters(index_of_point);
              calculateSteps(index_of_point+1);
              prepareMovement(0, steps_to_make_x[index_of_point]);
              prepareMovement(1, steps_to_make_y[index_of_point]);
              prepareMovement(2, steps_to_make_z[index_of_point]);
              runAndWait();
              
              Serial2.print("OK");
              sendEncodersData();
              break;
            case '3': // Wait time         
              Serial2.print("OK");   
              point_number = doc_rx["pt_no"];
              point_functions[point_number].func_type[0] = 1;
              point_functions[point_number].value[0] = doc_rx["value"];
              //
              Serial.print("func_type[pt][0]="); Serial.println(point_functions[point_number].func_type[0]);
              Serial.print("value[pt][0]="); Serial.println(point_functions[point_number].value[0]);
              //             
              break;   
            case '4': // Wait input
              Serial2.print("OK");
              point_number = doc_rx["pt_no"];
              point_functions[point_number].func_type[1] = 1;
              point_functions[point_number].value[1] = doc_rx["value"];
              point_functions[point_number].pin_no[1] = doc_rx["pin_no"];
              //
              Serial.print("func_type[pt][1]="); Serial.println(point_functions[point_number].func_type[1]);
              Serial.print("value[pt][1]="); Serial.println(point_functions[point_number].value[1]);
              Serial.print("pin_no[pt][1]="); Serial.println(point_functions[point_number].pin_no[1]);
              //              
              break;            
            case '5': // Set output
              Serial2.print("OK");
              point_number = doc_rx["pt_no"];            
              point_functions[point_number].func_type[2] = 1;
              point_functions[point_number].value[2] = doc_rx["value"];
              point_functions[point_number].pin_no[2] = doc_rx["pin_no"];
              //
              Serial.print("func_type[pt][2]="); Serial.println(point_functions[point_number].func_type[2]);
              Serial.print("value[pt][2]="); Serial.println(point_functions[point_number].value[2]);
              Serial.print("pin_no[pt][2]="); Serial.println(point_functions[point_number].pin_no[2]);   
              //
              break;            
            case '6':
              resetNumberOfTurns();
              break;
            case '7':
              gripper_state = doc_rx["state"];
              // String gripper_string;
              // gripper_state == 0? gripper_string = "OFF" : gripper_string = "ON"; 
              // String message = "Gripper: "; message.concat(gripper_string);
              // showOnScreen(message);            
              pinMode(SERVO_PIN, OUTPUT);  
              digitalWrite(SERVO_PIN, gripper_state);
              break;      
            case '8':
              enable_cmd = doc_rx["enable"];             
              enableMotors();
              resetNumberOfTurns();
              readEncoders();
              fi_array[0] = totalAngle[0];
              fi_array[1] = totalAngle[1];
              fi_array[2] = totalAngle[2];
              break;
            case '9':
                showOnScreen("Interpolating...");
                SD.begin(53);
                my_file = SD.open("testtest.txt", FILE_READ);
                if(!my_file) {
                  showOnScreen("Cannot read\nthe file");
                  break;
                }
                uint16_t file_position = 0;
                uint16_t i = 0;
                uint16_t n = 8; // interval time
                int velocity_1 = 0;
                int velocity_2 = 0;
                int velocity_3 = 0;
                uint16_t duration = 0;
                uint16_t interval_time = millis();
                uint16_t total_time = millis();
                uint16_t total_duration = 0;
                uint16_t movement_finish_time = 6400;

                stepper1.setTargetPositionRelativeInSteps(20000);
                stepper2.setTargetPositionRelativeInSteps(20000);
                stepper3.setTargetPositionRelativeInSteps(20000);

                while (total_duration < movement_finish_time){

                  stepper1.processMovement();
                  stepper2.processMovement();
                  stepper3.processMovement();

                  total_duration = millis() - total_time;
                  duration = millis() - interval_time;
                  
                  if (duration >= n) {
                    interval_time = millis();
                    readSingleIntervals(velocities, file_position);
                    velocity_1 = velocities[0];
                    velocity_2 = velocities[1];
                    velocity_3 = velocities[2];

                    stepper1.setCurrentPositionInSteps(0);
                    stepper2.setCurrentPositionInSteps(0);
                    stepper3.setCurrentPositionInSteps(0);

                    if (velocity_1 < 0)
                      digitalWrite(X_DIR_PIN, 1);
                    else
                      digitalWrite(X_DIR_PIN, 0);
                    if (velocity_2 < 0)
                      digitalWrite(Y_DIR_PIN, 1);
                    else
                      digitalWrite(Y_DIR_PIN, 0);
                    if (velocity_3 < 0)
                      digitalWrite(Z_DIR_PIN, 1);
                    else
                      digitalWrite(Z_DIR_PIN, 0);        
                    stepper1.setSpeedInStepsPerSecond(abs(velocity_1));
                    stepper2.setSpeedInStepsPerSecond(abs(velocity_2));
                    stepper3.setSpeedInStepsPerSecond(abs(velocity_3));
                    i++;
                  }
                }
              receive_in_progress = false;
              memset(receivedChars, 0, sizeof(receivedChars));  // clear the variable where read bytes are being written into
              showOnScreen("Waiting for\ncommand...");
              break;
            default:
              break;                            
          }
        }
        memset(receivedChars, 0, sizeof(receivedChars));  // clear the variable where read bytes are being written into
      }
      else if (mode == '#'){  // '#' is 35 in ASCII, end of transmission
        // String message = String("Waiting for \ncommand...\nProgram status:\n"); if (start) message.concat("start"); else message.concat("stop");
        // showOnScreen(message);
        receive_in_progress = false;
        memset(receivedChars, 0, sizeof(receivedChars));  // clear the variable where read bytes are being written into
      }
      //memset(receivedChars, 0, sizeof(receivedChars));  // clear the variable where read bytes are being written into
      //receive_in_progress = false;
      
  } while((millis() - receive_time < TIMEOUT) && receive_in_progress);
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

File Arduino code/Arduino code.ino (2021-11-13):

//    2021 DELTA robot software
//    Jakub Wrona & Grzegorz Radziwiłko
//    FOR NON COMMECIAL USE ONLY
//    Written in cooperation with Wroclaw University of Science and Technology under supervision of Dr. inż Krysztof Chrapek


//using namespace std;
#include <math.h>
#include <Wire.h>
#include <stdio.h>

#include "inverse_kin.h"
#include "multiplexer.h"


// For RAMPS 1.4  - PIN numbers for motors are defined by the hardware of RAMPS 1.4 board
// if necessairly, up to 5 motor slots are avaliable, for further pinout look into RAMPS1.4 datasheet

#define STEP_PIN_1         54
#define DIR_PIN_1          55
#define ENABLE_PIN_1       38
#define STEP_HIGH_1             PORTF |=  0b00000001; //lub 1 bit port C
#define STEP_LOW_1              PORTF &= ~0b00000001;
#define TIMER_INTERRUPT_1_ON    TIMSK3 |=  (1<<OCIE3A);
#define TIMER_INTERRUPT_1_OFF   TIMSK3 &= ~(1<<OCIE3A);

#define STEP_PIN_2         60
#define DIR_PIN_2          61
#define ENABLE_PIN_2       56
#define STEP_HIGH_2             PORTF |=  0b01000000; // lub bit 7 port c
#define STEP_LOW_2`             PORTF &= ~0b01000000;
#define TIMER_INTERRUPT_2_ON    TIMSK4 |=  (1<<OCIE4A);
#define TIMER_INTERRUPT_2_OFF   TIMSK4 &= ~(1<<OCIE4A);

#define STEP_PIN_3         46
#define DIR_PIN_3          48
#define ENABLE_PIN_3       62
#define STEP_HIGH_3             PORTL |=  0b00001000; // 3 bit port d
#define STEP_LOW_3              PORTL &= ~0b00001000;
#define TIMER_INTERRUPT_3_ON    TIMSK5 |=  (1<<OCIE5A);
#define TIMER_INTERRUPT_3_OFF   TIMSK5 &= ~(1<<OCIE5A);

#define START_PROGRAM_PIN  11 // PIN NA KTÓRY DAMY SYGNAŁ STARTU PROGRAMU 

#define MAX_NUM_OF_POINTS  100

#define MICROSTEPPING      16
#define STEPS_PER_REV      200

#define POINTS_DENSITY 4        //How many points for 1 cm of distance traveled 

#define MEMORY_SAFETY_MARIGIN 10  //[%]  allocate x% more memmory than aproximated 



//define global variables 
const double STEP_ANGLE = 360 / STEPS_PER_REV;
int program_length=0; 
int program_converted_length=0;
int program_start=0;
float previous_angles[3]={10,20,30};
float previous_position[3]= {0,0,-220};        
float speed_override =1;
float acc_override =1; 


///////////////////////  STRUCTURES AND CLASSES ///////////////////////

struct PositionData
{
  float abc[3]={0,0,0};                     //angle data [deg]
  float xyz[3]={0,0,0};                     //position data [mm] 
};

//Structure containing data about possible movement parameters of the motors 
struct MotionParam
{

  unsigned int min_interval=300;           //max speed - !!EXPERIMENTAL VALUE!!
  unsigned int acceleration_coef=8000;      //coefficient definig acceleration - !!EXPERIMENTAL VALUE!!

  float user_defined_speed_override=1;      //from GUI, [0-1]
  float user_defined_acc_override=1;        //from GUI, [0-1]

  float safety_override=1;                  //from safety measures like creating 'slow movement space' [0-1]

};

//Structure to contain movement point data 
struct Point
{
  byte index_of_point=NULL;         //point number in the program 
  byte interpolation=NULL;          //0=JOINT  1=LINEAR ... 2=CIRCULAR if implemented 
  byte speed=100;                   // [0-100%]
  byte acc=100;                     // [0-100%]
  float xyz[3]={0,0,0};             //x data [mm]
};

//Structure to contain movement point data after convertion
struct PointConverted
{
  unsigned int other_info [3];                //[0] - interpolation: 0=JOINT;  1=LINEAR;      [1] - movement mode - 0=accelerate; 1=mentain speed; 2=deaccelerate;    [2]- point of origin;  
  int steps[3]={0,0,0};                      //number of steps motor3 
  bool state_flag=false;                     //variable monitoring if efector already reached given point 
};

//Class for dealing with all the data and actions regarding stepper motors
class Motor
{
  public:

    int dirPin = 0;                   // Direction
    int stepPin = 0;                  // step
    int enablePin = 0;
    bool motor_state = false;         // variable for monitoring step pin state from previous cycle
    bool motion_done = false; 
    int steps_done = 0;               // variable for monitoring number of steps done by the motor in a given 'move' command
    int steps_required = 0;           // variable containing information about required amount of steps in a given 'move' command
    int timerNumber = 0;              // Identyfication number of the counter/timer that operate interrupt rutines for the PWM driving motor   ! must be 3, 4 or 5
    int conv_point=0;         // currently moving to this point 
    unsigned int comp_reg_value=0;    //register value that timer compares to 
    unsigned int slope_len_iterator=0;      //iterator for measuring how many steps there are in slope 
    unsigned int interpolation=0;   //
    unsigned int movement_mode=0;   // accelerate / mentain speed / slow down 
    unsigned int movement=0;              
    unsigned int min_interval=0;            //top speed 
    unsigned int slope_len=0;

  

    // constructor - setting pinout
    Motor(int dir_pin, int step_pin, int enable_pin, int timer_number)
    {
      dirPin=dir_pin;           // Direction
      stepPin=step_pin;         // step 
      enablePin=enable_pin;     // enable motors
      timerNumber= timer_number;
      pinMode(enablePin, OUTPUT);
      pinMode(dirPin, OUTPUT);
      pinMode(stepPin, OUTPUT);
    }
    
    // function to start moving in given direction
    void move (bool dir, int steps, int converted_point_num, unsigned int minimal_interval, unsigned int acceleration_coef, unsigned int current_interpolation, unsigned int current_movement_mode)
    {
      motion_done=false;
      steps_required = 2*steps;
      conv_point = converted_point_num; 
      interpolation = current_interpolation;
      movement_mode = current_movement_mode;
      comp_reg_value =  acceleration_coef;
      min_interval = minimal_interval;
      slope_len=0;
      unsigned int reg= comp_reg_value;
      
      while(1)          //calculate slope_len
      { 
        reg= reg - (2*reg) / (4 * slope_len + 1);
        slope_len++;
        if (min_interval > reg ) {break;}
      }        
      
      if (dir)                                                         // set dir pin state accordingly to provided direction variable
      {
        digitalWrite(dirPin, HIGH);
      }else
      {
        digitalWrite(dirPin, LOW);
      }

      switch (timerNumber)
      {
        case 3:
          cli();                          //disable interrupts for modifiaction
          TCNT3 = 0;                      // set zero as counter value
          OCR3A = comp_reg_value;    // set compare register value
          TIMSK3 |= (1 << OCIE3A);        // enable interrupts for this timer/counter
          sei();                          //enable interrupts for normal operation
          break;
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

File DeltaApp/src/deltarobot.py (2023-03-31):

import VerticesCoordinates
from collisionException import *
from math import sqrt, sin, cos, atan


# angle limits used in limiting the movement
OUT_OF_RANGE_ANGLE_LOW = -0.5235987756
OUT_OF_RANGE_ANGLE_HIGH = 1.5707963268
ELBOW_JOINT_WIDTH = 45
LINK_OFFSET = ELBOW_JOINT_WIDTH / 2
SQRT_3 = sqrt(3)
SQRT_3_2 = sqrt(3) / 2

class DeltaRobot():

    def __init__(self):

        self.vert_coords = VerticesCoordinates.VerticesCoordinates()
        self.initializeCoords()
        # geometry of the robot
        self.sb = 375  # 25mm is subtracted from 400 because the axes are mounted with 25mm offset  # 567  # length of the Side of the Base triangle in mm (sb)
        self.sp = 76  # length of the Side of the effector (Plate) triangle in mm (sp)
        self.Length = 200  # 524  # length of the biceps in mm (L)
        self.length = 281  # 1244  # length of the forearm in mm (l)
        self.Length2 = self.Length ** 2  # square of Length
        self.length2 = self.length ** 2  # square of length
        self.wb = 1 / 3 * SQRT_3_2 * self.sb  # distance from the center of the Base to the side of the triangle
        self.ub = 2 * self.wb  # distance from the center of the Base to the side of the triangle
        self.wp = 1 / 3 * SQRT_3_2 * self.sp  # distance from the center of the effector (Plate) to the vertex of the triangle
        self.up = 2 * self.wp
        self.a = self.wb - self.up
        self.b = self.sp / 2 - SQRT_3_2 * self.wb
        self.c = self.wp - 1 / 2 * self.wb
        self.TCP = [0, 0, -100]  # offset for the TCP
        self.z_limit = -430

        # safe areas - legs
        self.safe_leg_1 = [-0.866 * self.ub - 25, -self.wb - 25, -0.866 * self.ub + 25, -self.wb + 25]
        self.safe_leg_2 = [0.866 * self.ub - 25, -self.wb - 25, 0.866 * self.ub + 25, -self.wb + 25]
        self.safe_leg_3 = [-25, self.ub - 25, 25, self.ub + 25]

        # variables
        self.fi = [0, 0, 0]

        # vectors for elbow joints Ai
        self.A1 = [0.0, 0.0, 0.0]
        self.A2 = [0.0, 0.0, 0.0]
        self.A3 = [0.0, 0.0, 0.0]

        # vectors for base joints Bi in base frame {B}
        self.B1 = [0, -self.wb, 0]
        self.B2 = [SQRT_3_2 * self.wb, 1 / 2 * self.wb, 0]
        self.B3 = [-SQRT_3_2 * self.wb, 1 / 2 * self.wb, 0]

        # vectors for effector joints Pi in effector frame {P}
        self.P1 = [0, -self.up, 0]
        self.P2 = [self.sp / 2, self.wp, 0]
        self.P3 = [-self.sp / 2, self.wp, 0]

        # coordinates of the base vertices (for animation)
        self.Bvx = [-self.sb / 2, 0, self.sb / 2, -self.sb / 2]
        self.Bvy = [-self.wb, self.ub, -self.wb, -self.wb]
        self.Bvz = [0, 0, 0, 0]

    def initializeCoords(self):
        """ Initialize vertices coordinates to 0 """
        self.vert_coords.coordinates_x =[[0.0], [0.0], [0.0], [0.0], [0.0], [0.0], [0.0], [0.0]]
        self.vert_coords.coordinates_y =[[0.0], [0.0], [0.0], [0.0], [0.0], [0.0], [0.0], [0.0]]
        self.vert_coords.coordinates_z =[[0.0], [0.0], [0.0], [0.0], [0.0], [0.0], [0.0], [0.0]]

    def calculateIPK(self, xyz):
        """ Calculate inverse kinematics based on input coordinates. Input is a tuple (x,y,z) """
        x = xyz[0] - self.TCP[0]
        y = xyz[1] - self.TCP[1]
        z = xyz[2] - self.TCP[2]

        # If z>-70 then it's not a viable configuration of robot
        if z + self.TCP[2] > -70 or z + self.TCP[2] < self.z_limit:
            print("The coordinates are out of range!")
            raise TypeError

        # constants used to calculate Inverse Kinematics
        Ei, Fi, Gi = self.calculateConstants((x, y, z))
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

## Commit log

2021-10-16 Arduino code and venv folder
2021-10-16 Arduino receive json file
2021-10-19 Arduino receive point by point
    New arduino program to test if receiving point by point json is possible (or doable)
2021-10-19 Arduino - point by point receive two points
    Receiving two points in seperate messages
2021-10-19 Arduino - changes in linear motion execution
    Added function that executes motion in case of linear movement
2021-10-20 Arduino- part of joint interpolation
2021-10-21 Arduino- joint done
2021-10-22 Arduino receive point by point update
2021-10-29 ArduinoDebbug - not done
    Optymised to work on Ardu UNO
2021-10-30 Arduino debugging - almost done
    Values are wrong
    [Arduino code.ino, inverse_kin.h]
2021-11-07 Added enable, disable, teach-in buttons and gyro data plotting
2021-11-07 Arduino
    code for UNO, uncomment interrupts for mega
2021-11-07 Arduino 2.0
    Major rework
    [Arduino code.ino]
2021-11-09 Motor_1 TESTv2
    motor1 should acc and slow down well
2021-11-10 Added teach-in functionality, continuous position update, joints' angles plotting and available COMs list
2021-11-11 Created macros for interrupt control and stepping
2021-11-13 Working area visualisation, minor upgrades, arduino communication still in work
2021-11-18 Building up the program
    Added encoders calibration and changed the way of communicating with Python
2021-11-18 Arduino communication almost done (sending functions not yet implemented)
2021-12-12 Double the framerate
2022-01-25 Create Kinematics equations
2022-03-17 Small fixes and added functionality
    Additional robot program functionality now works (wait time, wait input, set output).
    [deltagui.py]
2022-03-18 Bug fix
    Fixed a bug with non-existing config.txt file
    [deltagui.py]
2022-03-18 Additional functionality support
    Additional functions in robot's program can now be edited. They are protected against wrong input and are working as intended.
    [deltagui.py]
2022-04-11 Added gripper support and simple interpolation
    Gripper or other output control is now supported from the GUI, default output pin is 63. Interpolation can be performed, reading steppers speed from sd card (values have to be generated beforehand), although it's still quite buggy and definitely shouldn't be a final solution.
    [delta_main_code.ino]
2022-04-11 Added gripper support and fixed upload bug
    Gripper can now be opened or closed manually (before it was only possible while in executing a program). There was a bug with uploading the robot program to the controller, which has been fixed by adding timeout while waiting for response.
    [deltagui.py]
